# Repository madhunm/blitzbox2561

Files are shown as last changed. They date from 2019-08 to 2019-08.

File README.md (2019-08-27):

# blitzbox2561
mini-sized ECU for speeduino firmware (5x5 cm)

2 injectors<br/>
2 active ignition coils or 1 passive ignition coil with separate ground plane<br/>
1 crankshaft sensor with VR-conditioner<br/>
6 analog inputs: CLT, IAT, TPS, BAT, Wideband Lambda, onboard MAP (4250 or 6400)<br/>

1 fuel pump out<br/>

1 idle valve out<br/>
1 tacho out<br/>
4 free and non-wired general purpose I/O's<br/>
USB programming interface with PL2303SA (Tunerstudio)<br/>

all in/outputs can be programmed different

[Link to the original speeduino project](https://www.speeduino.com "speeduino homepage")

<p align="center">
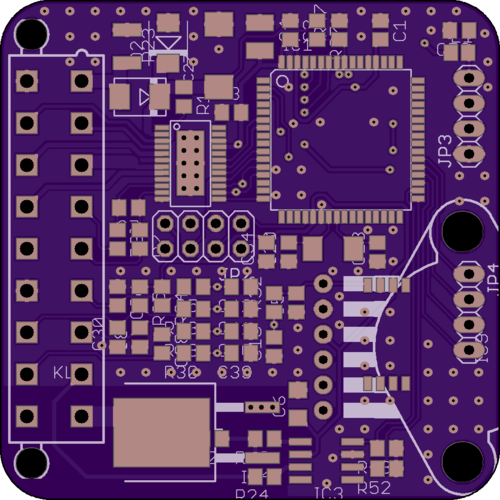
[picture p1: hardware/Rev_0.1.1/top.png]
  
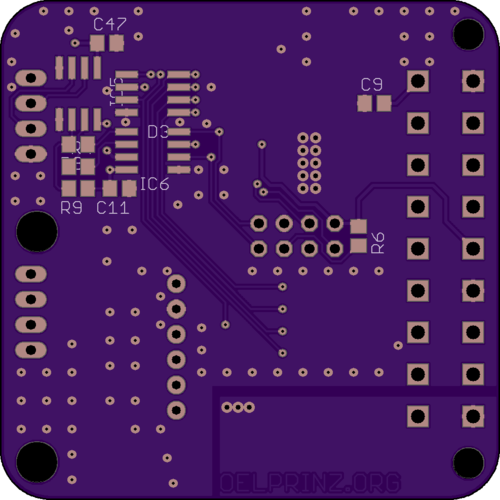
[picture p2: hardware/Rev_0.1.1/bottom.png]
  <br/>
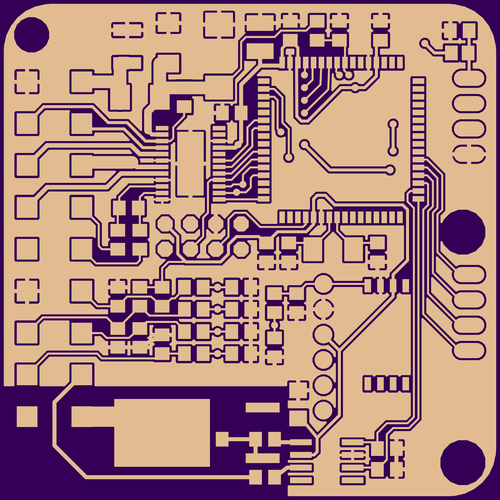
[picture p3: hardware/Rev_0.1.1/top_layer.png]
    
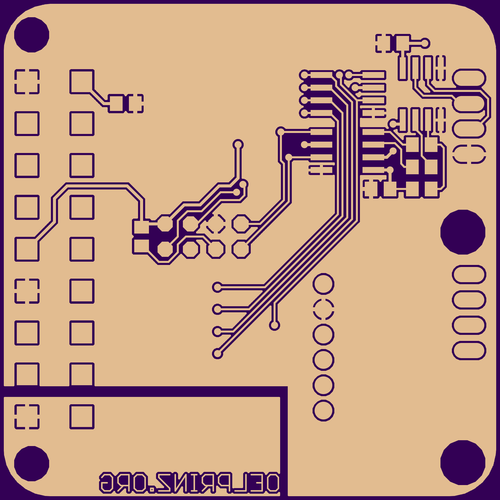
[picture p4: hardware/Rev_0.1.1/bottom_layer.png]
  
</p>

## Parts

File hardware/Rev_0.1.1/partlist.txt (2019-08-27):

Partlist

Exported from blitzbox.brd at 27.08.19 10:24

EAGLE Version 8.2.0 Copyright (c) 1988-2017 Autodesk, Inc.

Assembly variant: 

Part     Value                Package   Library             Position (mil)        Orientation

C1       100n                 C0805     rcl                 (1500 1850)           R270
C2       100n                 C0805     rcl                 (1143.75 1850)        R270
C3       100n                 C0805     rcl                 (912.5 1525)          R0
C4       22u                  C1210     rcl                 (1025 1825)           R270
C5       1n                   C0805     rcl                 (1168.75 775)         R90
C6       22u                  C1206     rcl                 (1175 375)            R90
C7       1n                   C0805     rcl                 (506.25 1150)         R180
C8       1n                   C0805     rcl                 (550 637.5)           R90
C9       1n                   C0805     rcl                 (493.75 1562.5)       MR0
C11      100n                 C0805     rcl                 (1500 1225)           MR180
C16      220n                 C0805     rcl                 (1081.25 600)         R90
C20      18p                  C0805     rcl                 (1137.5 975)          R90
C23      18p                  C0805     rcl                 (1487.5 975)          R90
C27      TAJD336*035#NJ       SMC_D     rcl                 (862.5 1750)          R90
C28      1n                   C0805     rcl                 (637.5 612.5)         R270
C30      1n                   C0805     rcl                 (462.5 637.5)         R90
C34      100n                 C0805     rcl                 (1050 975)            R90
C36      1n                   C0805     rcl                 (462.5 800)           R270
C39      220n                 C0805     rcl                 (950 575)             R180
C40      220n                 C0805     rcl                 (950 662.5)           R180
C41      1u                   C0805     rcl                 (950 750)             R180
C42      1u                   C0805     rcl                 (950 837.5)           R180
C47      1u                   C0805     rcl                 (1550 1800)           MR0
C50      1n                   C0805     rcl                 (1812.5 1850)         R180
D1       MURS120              MURS120   murs120             (550 1587.5)          R0
D2       SMBJ22A              SMBJ      diode               (662.5 1800)          R90
D3       DA112S1              SO08      st-microelectronics (1368.75 1600)        MR90
IC1      ATMEGA2561-16AU      TQFP64    atmel-2005          (1343.75 1418.75)     R0
IC2      TLE8080              TLE8080   tle8080             (750 1325)            R270
IC3      MCP14E10             SO-08     mcp14e10            (1287.5 150)          R90
IC4      FGB3056_F085         TO263     FGB3056_F085        (775 262.5)           R90
IC5      USB6B1               SO08      st-microelectronics (1662.5 1600)         MR180
IC6      PL2303SA             SO-08     PL2303SA            (1368.75 1375)        MR90
IC8      MPXH6400AC6T1        MPXH6400  MPXH6400            (1525 650)            R270
IC9      MPX4250              MPX4250   mpx4250             (1825 600)            R270
JP2                           2X04      pinhead             (800 1037.5)          R180
JP3      USB                  1X04      pinhead             (1850 1512.5)         R90
JP4                           1X04      pinhead             (1850 737.5)          R270
L1       L0805C100MDWIT       FB805     dp_devices          (1812.5 1762.5)       R0
Q1       ABM3-16.000MHZ-D2Y-T ABM3      ABM3                (1313.1282 987.42384) R0
R1       1k                   R0805     rcl                 (725 1587.5)          R270
R2       0R(NC)               R0805     rcl                 (837.5 237.5)         R180
R3       10k                  R0805     rcl                 (462.5 1025)          R270
R4       27R                  R0805     rcl                 (1662.5 1312.5)       MR0
R5       1k                   R0805     rcl                 (762.5 837.5)         R180
R6       10k                  R0805     rcl                 (556.25 1037.5)       MR270
R7       10k                  R0805     rcl                 (550 1025)            R270
R8       27R                  R0805     rcl                 (1662.5 1400)         MR180
R9       1k5*                 R0805     rcl                 (1662.5 1225)         MR180
R10      220R                 R0805     rcl                 (1043.75 237.5)       R180
R13      1k                   R0805     rcl                 (762.5 750)           R180
R18      1k                   R0805     rcl                 (762.5 662.5)         R180
R23      B72530V1140S262      CT/CN1210 varistor            (500 1787.5)          R270
R24      220R                 R0805     rcl                 (1043.75 87.5)        R180
R30      1k                   R0805     rcl                 (762.5 575)           R180
R32      1k                   R0805     rcl                 (1081.25 775)         R90
R34      2k49                 R0805     rcl                 (637.5 800)           R270
R35      2k49                 R0805     rcl                 (550 800)             R270
R37      39k                  R0805     rcl                 (1250 1850)           R270
R47      10k                  R0805     rcl                 (1337.5 1850)         R90
R52      39k                  R0805     rcl                 (1525 118.75)         R180
R58      39k                  R0805     rcl                 (1525 200)            R180
X2       5566-18              5566-18   con-molex           (212.5 987.5)         R90

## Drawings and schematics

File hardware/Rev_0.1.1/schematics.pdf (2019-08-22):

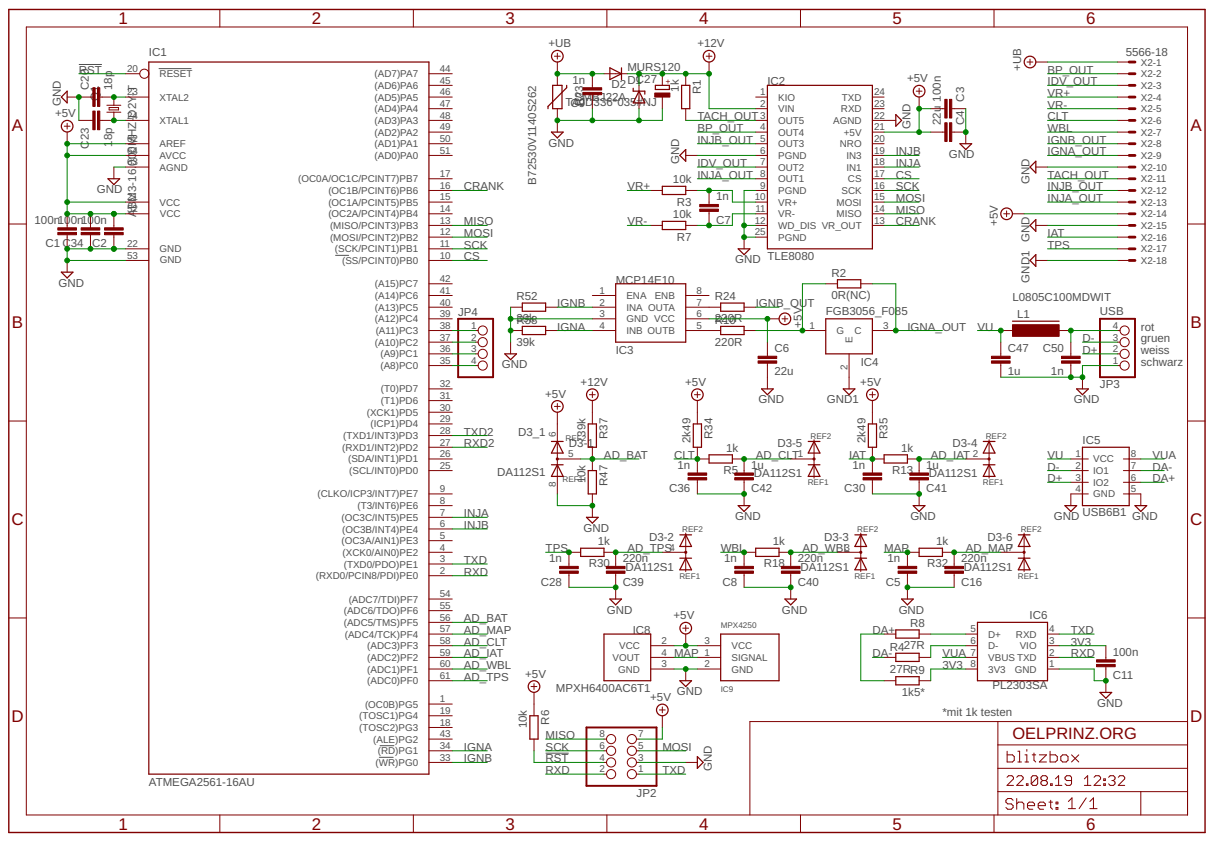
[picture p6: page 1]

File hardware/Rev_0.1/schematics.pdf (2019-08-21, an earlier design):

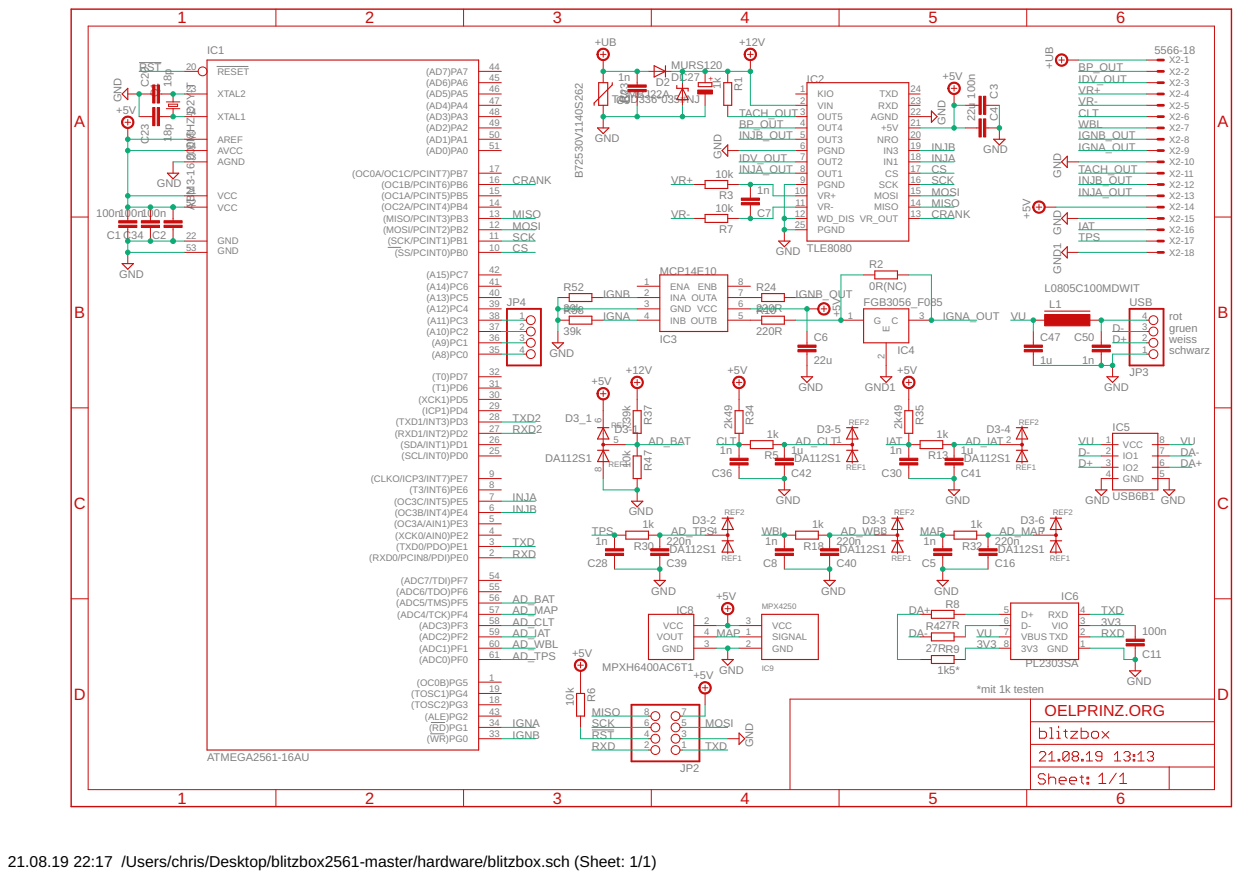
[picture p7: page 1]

21.08.19 22:17 /Users/chris/Desktop/blitzbox2561-master/hardware/blitzbox.sch (Sheet: 1/1)

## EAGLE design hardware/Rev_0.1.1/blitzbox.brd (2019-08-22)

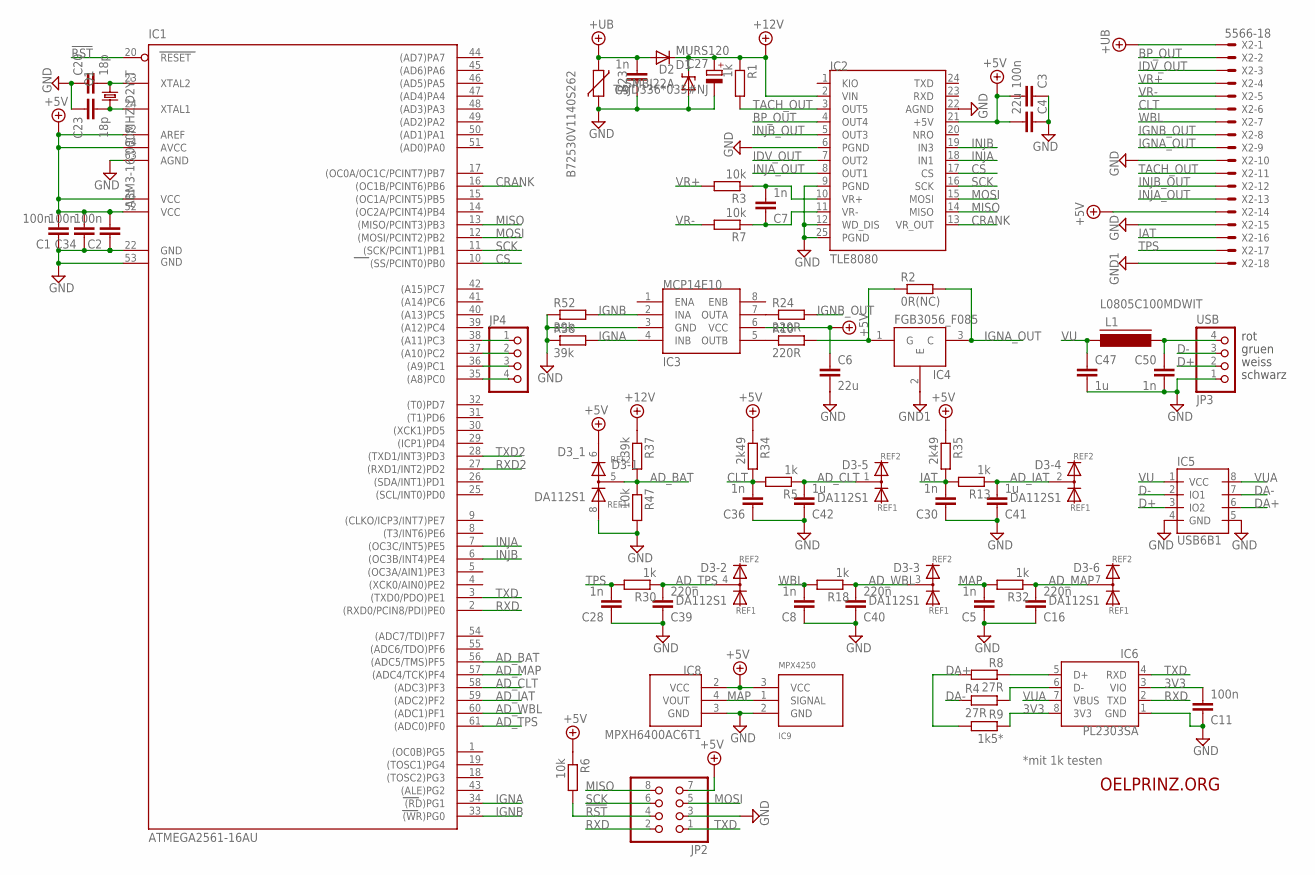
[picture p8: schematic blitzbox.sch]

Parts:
C1, C2, C3, C11, C34: 100n; C0805
C4: 22u; C1210
C5, C7, C8, C9, C28, C30, C36, C50: 1n; C0805
C6: 22u; C1206
C16, C39, C40: 220n; C0805
C20, C23: 18p; C0805
C27: TAJD336*035#NJ; SMC_D
C41, C42, C47: 1u; C0805
D1: MURS120
D2: SMBJ22A; SMBJ
D3: DA112S1; SO08
IC1: ATMEGA2561-16AU; TQFP64
IC2: TLE8080
IC3: MCP14E10; SO-08
IC4: FGB3056_F085; TO263
IC5: USB6B1; SO08
IC6: PL2303SA; SO-08
IC8: MPXH6400AC6T1; MPXH6400
IC9: MPX4250
JP2: PINHD-2X4; 2X04
JP3: USB; 1X04
JP4: PINHD-1X4; 1X04
L1: L0805C100MDWIT; FB805
Q1: ABM3-16.000MHZ-D2Y-T; ABM3
R1, R5, R13, R18, R30, R32: 1k; R0805
R2: 0R(NC); R0805
R3, R6, R7, R47: 10k; R0805
R4, R8: 27R; R0805
R9: 1k5*; R0805
R10, R24: 220R; R0805
R23: B72530V1140S262; CT/CN1210
R34, R35: 2k49; R0805
R37, R52, R58: 39k; R0805
X2: 5566-18

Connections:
3V3: C11.2, IC6.3 (VIO), IC6.8 (3V3), R9.1
!RST: IC1.20 (RESET), JP2.4, R6.2
+5V: C1.2, C2.2, C3.2, C4.2, C6.1, C34.2, D3.6 (REF2), IC1.21 (VCC), IC1.52 (VCC1), IC1.62 (AREF), IC1.64 (AVCC), IC2.21 (+5V), IC3.6 (VCC), IC8.2 (VCC), IC9.3 (VCC), JP2.7, R6.1, R34.1, R35.1, X2.14
+5VU: C50.1, JP3.4, L1.2
+12V: C27.+, D1.2 (C), D2.C, IC2.2 (VIN), R1.1, R37.1
+UB: C9.2, D1.1 (A), R23.2, X2.1
AD_BAT: D3.5 (K), IC1.56 ((ADC5/TMS)PF5), R37.2, R47.1
AD_CLT: C42.2, D3.1 (K), IC1.58 ((ADC3)PF3), R5.1
AD_IAT: C41.2, D3.2 (K), IC1.59 ((ADC2)PF2), R13.1
AD_MAP: C16.2, D3.7 (K), IC1.57 ((ADC4/TCK)PF4), R32.1
AD_TPS: C39.2, D3.4 (K), IC1.61 ((ADC0)PF0), R30.1
AD_WBL: C40.2, D3.3 (K), IC1.60 ((ADC1)PF1), R18.1
BP_OUT: IC2.4 (OUT4), X2.2
CLT: C36.2, R5.2, R34.2, X2.6
CRANK: IC1.16 ((OC1B/PCINT6)PB6), IC2.13 (VR_OUT)
CS: IC1.10 ((SS/PCINT0)PB0), IC2.17 (CS)
D+: IC5.3 (IO2), JP3.2
D-: IC5.2 (IO1), JP3.3
DA+: IC5.6 (IO2), R8.2, R9.2
DA-: IC5.7 (IO1), R4.1
GND: C1.1, C2.1, C3.1, C4.1, C5.1, C6.2, C8.1, C9.1, C11.1, C16.1, C20.1, C23.1, C27.-, C28.1, C30.1, C34.1, C36.1, C39.1, C40.1, C41.1, C42.1, C47.2, C50.2, D2.A, D3.8 (REF1), IC1.22 (GND), IC1.53 (GND1), IC1.63 (AGND), IC2.6 (PGND), IC2.9 (PGND), IC2.12 (WD_DIS), IC2.22 (AGND), IC2.25 (PGND), IC3.3 (GND), IC5.4 (GND), IC5.5 (GND), IC6.1 (GND), IC8.3 (GND), IC9.2 (GND), JP2.3, JP3.1, R23.1, R47.2, R52.1, R58.1, X2.10, X2.15
GND1: IC4.2 (E), X2.18
IAT: C30.2, R13.2, R35.2, X2.16
IDV_OUT: IC2.7 (OUT2), X2.3
IGN: IC4.1 (G), R2.1, R10.2
IGNA: IC1.34 ((RD)PG1), IC3.4 (INB), R58.2
IGNA_OUT: IC4.3 (C), R2.2, X2.9
IGNB: IC1.33 ((WR)PG0), IC3.2 (INA), R52.2
IGNB_OUT: R24.2, X2.8
INJA: IC1.7 ((OC3C/INT5)PE5), IC2.18 (IN1)
INJA_OUT: IC2.8 (OUT1), X2.13
INJB: IC1.6 ((OC3B/INT4)PE4), IC2.19 (IN3)
INJB_OUT: IC2.5 (OUT3), X2.12
MAP: C5.2, IC8.4 (VOUT), IC9.1 (SIGNAL), R32.2
MISO: IC1.13 ((MISO/PCINT3)PB3), IC2.14 (MISO), JP2.8
MOSI: IC1.12 ((MOSI/PCINT2)PB2), IC2.15 (MOSI), JP2.5
unnamed: C7.1, IC2.11 (VR-), R7.1
unnamed: IC3.5 (OUTB), R10.1
unnamed: IC6.6 (D-), R4.2
unnamed: IC6.5 (D+), R8.1
unnamed: IC1.38 ((A11)PC3), JP4.1
unnamed: IC1.37 ((A10)PC2), JP4.2
unnamed: IC1.36 ((A9)PC1), JP4.3
unnamed: IC1.35 ((A8)PC0), JP4.4
unnamed: C7.2, IC2.10 (VR+), R3.1
unnamed: IC3.7 (OUTA), R24.1
RXD: IC1.2 ((RXD0/PCIN8/PDI)PE0), IC6.2 (TXD), JP2.2
RXD2: IC1.27 ((RXD1/INT2)PD2)
SCK: IC1.11 ((SCK/PCINT1)PB1), IC2.16 (SCK), JP2.6
TACH_OUT: IC2.3 (OUT5), R1.2, X2.11
TPS: C28.2, R30.2, X2.17
TXD: IC1.3 ((TXD0/PDO)PE1), IC6.4 (RXD), JP2.1
TXD2: IC1.28 ((TXD1/INT3)PD3)
VR+: R3.2, X2.4
VR-: R7.2, X2.5
VU: C47.1, IC5.1 (VCC), L1.1
VUA: IC5.8 (VCC), IC6.7 (VBUS)
WBL: C8.2, R18.2, X2.7
XTAL1: C20.2, IC1.23 (XTAL2), Q1.1
XTAL2: C23.2, IC1.24 (XTAL1), Q1.2

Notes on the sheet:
rot
gruen
weiss
schwarz
OELPRINZ.ORG
*mit 1k testen

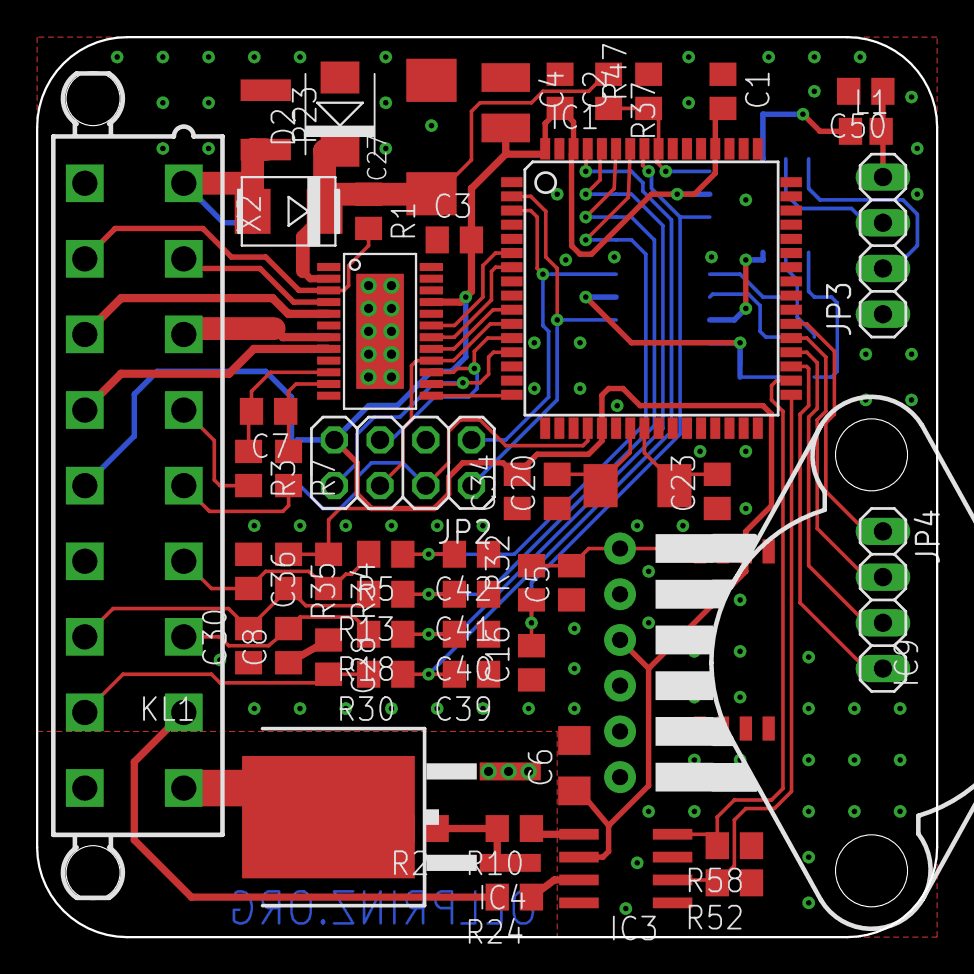
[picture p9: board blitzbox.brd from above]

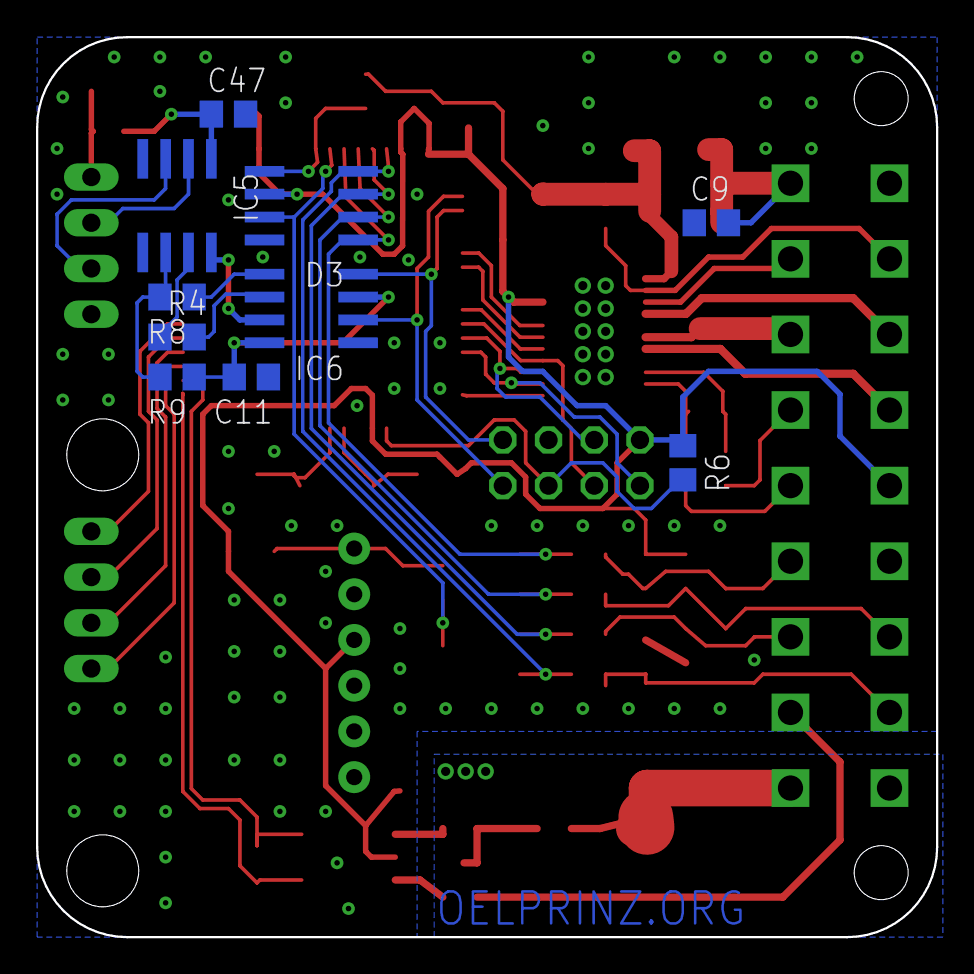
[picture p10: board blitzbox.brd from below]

Board: 2 copper layers, 50.0 x 50.0 mm, 63 parts (10 on the bottom side), 58 nets.
